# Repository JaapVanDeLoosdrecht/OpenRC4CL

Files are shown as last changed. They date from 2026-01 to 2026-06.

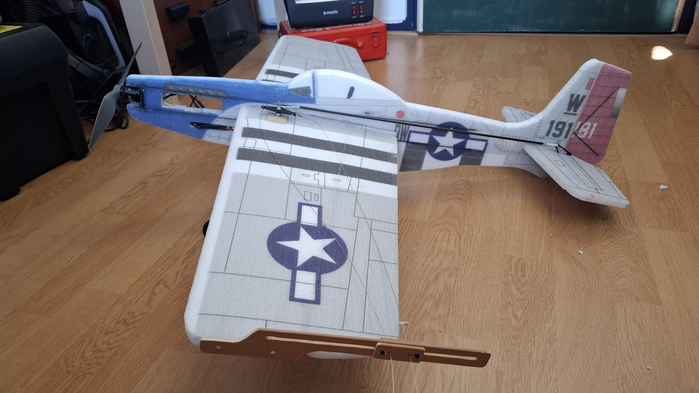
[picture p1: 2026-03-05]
photos/CL-E test model.jpg

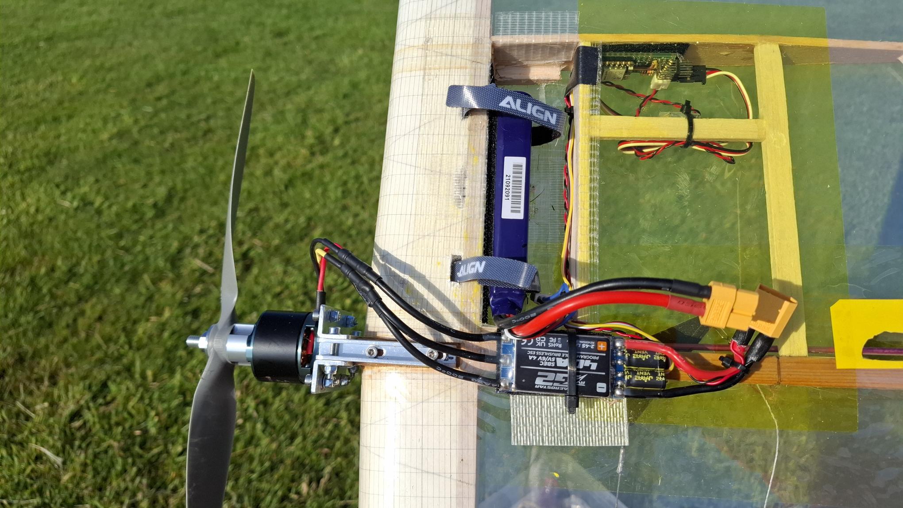
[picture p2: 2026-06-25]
photos/E-Combat 3.jpg

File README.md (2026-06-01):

# OpenRC4CL

Control Line (CL), also called U-Control, is a way of controlling model airplanes, see https://en.wikipedia.org/wiki/Control_line.

Low-cost DIY project based on low-cost ESP32C6s for expanding CL handles with Radio Control (RC) functions like throttle control, servos, timers, telemetry and failsafe.
Uses the ESP-NOW protocol transmitted via the 2.4 GHz Wi-Fi band.

One PCB for Tx, Rx and Timer.

The software is released as opensource under the MIT license.

Note this project is Work In Progress and is developed for ESP32 C6, does not need external antennas.

Feedback is welcome and I am open to ideas and/or collaboration.

See for discussion the (Dutch) Modelbouw forum https://www.modelbouwforum.nl/threads/openrc4cl-diy-lb-met-rc-functies.294026/ .

## NOTE: there are two PCBs:
- PCB V1 (4 channels) is tested
- PCB V2 is under design and not yet tested. It is smaller and for 2 channels.

## Functional overview OpenRC4CL.

Expanding CL handles with RC functions like throttle control, servos, timers, telemetry and failsafe.
Usage cases:

- Combat/trainer CL handle with throttle hold switch and small potmeter for setting throttle value between flights.
- Carrier/scale CL handle with continuous throttle 'trigger' control, throttle hold switch and 
  3 (two 3 states and one continuous) servo functions like for dropping hook, etc.
- etc.

Default servo pulse width [1000..2000] us @ 50 Hz, in software configurable.

Tx channels:

- 0: throttle potmeter
- 1: 3 position switch
- 2: potmeter or 3 position switch
- 3: potmeter or 3 position switch
- 4: potmeter or 3 position switch

Rx servo channels:

- 0: throttle
- 1: servo 1
- 2: servo 2
- 3: servo 3
- 4: servo 4

Special functions:

- kill switch on Tx
- check pairing Tx and Rx based on MAC address [planned soft MAC address]
- checksum on transmitted data
- failsafe if > 0.5 seconds connection lost OR TxBatt low:
  initiate throttle warning (like CLTimer) followed by stop engine and hold servos in last position
- telemetry with VBatt, VBatt low and RSI 
- throttle hold must be activated before Tx starts to transmit
- logging status and listing/setting configuration parameters of Tx andRx by bluetooth to smartphone
- Tx lipo voltage monitor (1 cell lipo) with low VBat warning
- low VBatt warning voltage setting (input potmeter) [3000..8*4350] mV, max 8S LiHV
- Rx ESC max 8S lipo voltage monitor, telemetry to Tx and beeper warning by low VBat
- max flight time parameter
- deadband throttle correction parameter
- exponential throttle curve (in software configurable) [planned]
- softstart throttle option (in software configurable) [planned]

Status codes for led and beeper (blink pulse in ms):
- Ok = 0 (off)
- WaitThrHold = 1000
- WaitConnection = 2000
- VBattLow and TxBattLow = 2000
- EndFlight = 4000
- Failsafe = 500
- Error = 200

## CLTimer [planned]

CLTimer is 'spinoff' project from components used for Tx and Rx projects in the OpenRC4CL repro.

Usage case: typical classic control line timer without remote RC functionality.

Inputs:

- parameters (analog input with potmeters):
	- delay start [0..60] secs
	- throttle level [0..100]%
	- runtime [0..8*60] secs
	- min VBatt [3000..8*4350] mV, max 8S LiHV
- VBatt (max 8S) (analog input)
- start/stop button (digital input)

Outputs:

- servo signal for ESC (analog output)
- status led (digital output)
- beeper (digital output)

Note if VBatt is not connected, only timer function avialable.

Phases (N and W are parameters configurable in software):  [WIP]

- connect battery and boot
- read parameters, log every 0.5 second parameters to serial monitor and BT 
- press button for 2 seconds to intiate 'ready_to_start', confirm with beep
- during ready_to_start
  - beep every 10 secs, last 10 sec every sec
  - abort ready_to_start if start button is pressed for 2nd time
    go to phase read parameters
- start engine and throttle timer, log every 0.5 second status to serial monitor and BT
- abort running if start button is (short) pressed for 2nd time
  go to phase read parameters
- W seconds before throttle timer expires OR if VBatt below min VBatt:
  issue for N (N < W) seconds throttle warnings (0.5 s half, 0.5 s normal throttle level) 
  (last W-N seconds full throttle level)
- stop engine 

Logging status by bluetooth or usb to smartphone or laptop.

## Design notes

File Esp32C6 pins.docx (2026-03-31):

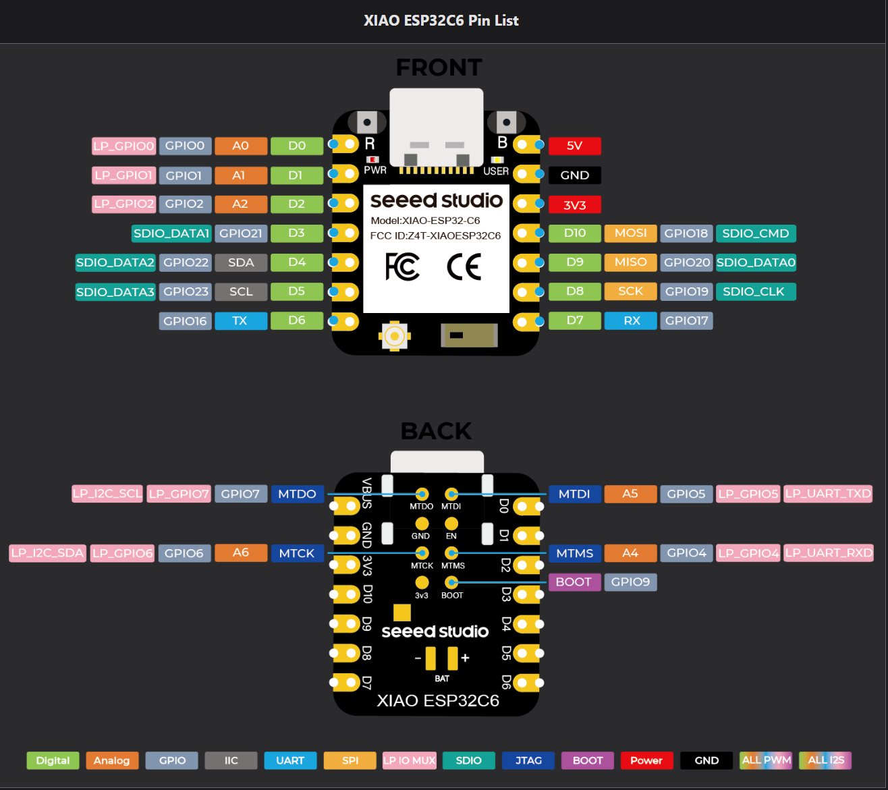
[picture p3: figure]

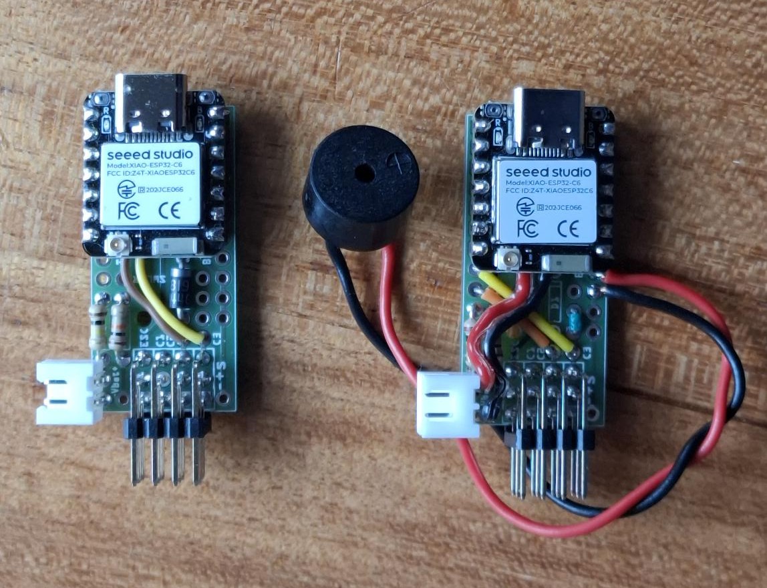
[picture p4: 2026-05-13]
photos/First Tx and Rx PCB V1.0.jpg

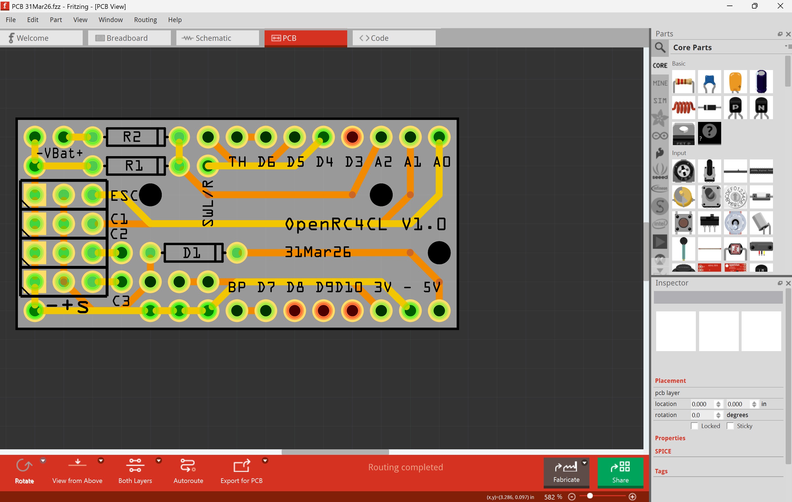
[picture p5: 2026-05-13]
photos/Fritzing PCB V1.0.jpg

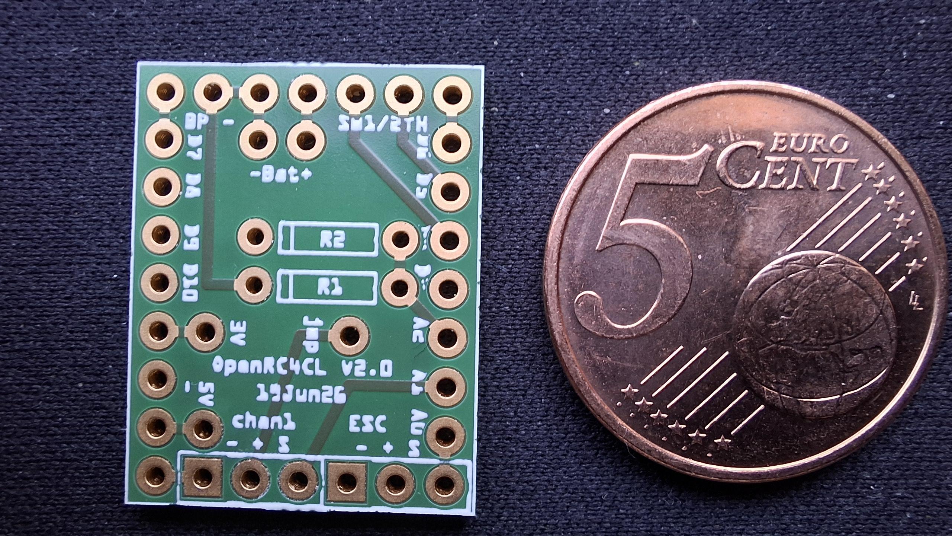
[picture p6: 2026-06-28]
photos/OpenRC4CL PCB V2.jpg

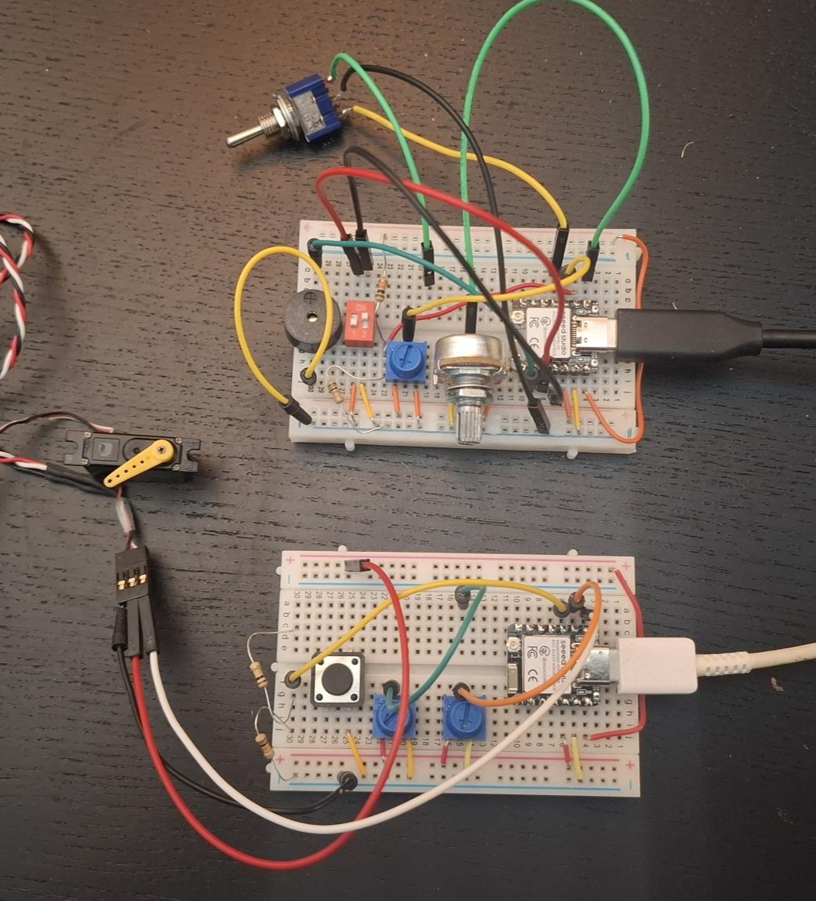
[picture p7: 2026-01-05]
photos/breadboard TxRx 15Dec25.jpg

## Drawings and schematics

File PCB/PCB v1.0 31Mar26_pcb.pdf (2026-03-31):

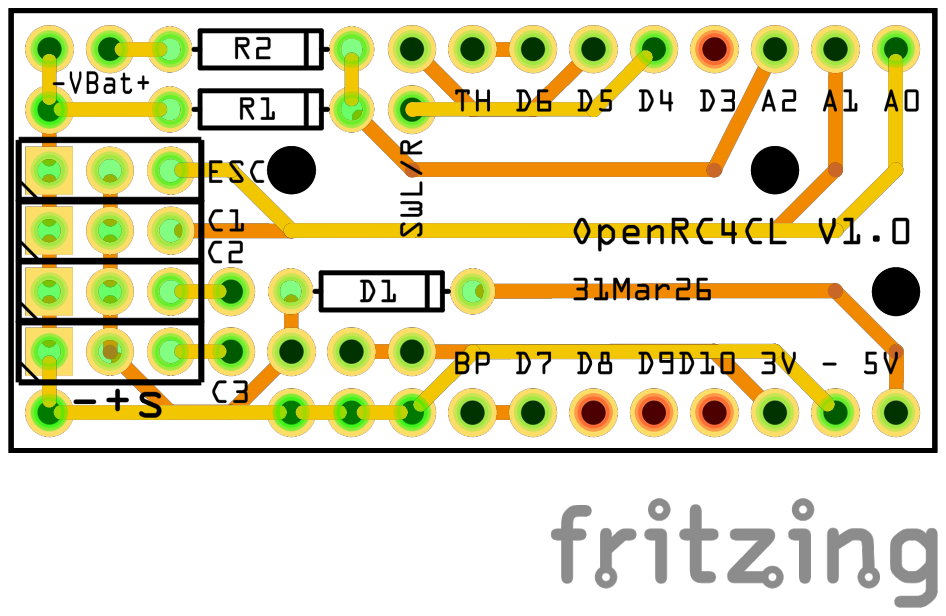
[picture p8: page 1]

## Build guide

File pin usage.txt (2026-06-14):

-----------------------------------------------------------------------
Pin usage PCB design V1.0:
Rx
- LED_BUILTIN: led Note LED_BUILTIN is reversed on C6
- A0: throttle=chan0 (output servo)
- A1: chan1 (output servo)
- A2: VBatt 8S lipo voltage monitor (input)
- D3:             
- D4:            
- D5:
- D6:
- D7:
- D8:
- D9: 
- D10:
- A4: chan2 (output servo)
- A5: chan3 (output servo)
- A6: chan4 (optional output servo, no PCM pad)

Tx:
- LED_BUILTIN: led: Note LED_BUILTIN is reversed on C6
- A0: throttle=chan0 (input potmeter)
- A1: 
- A2: Tx lipo voltage monitor (1 cell lipo) (input)
- D3:                                                                                                                                                                                                    
- D4: leftCh1  (input 3-pos switch)
- D5: rightCh1 (input 3-pos switch)
- D6: throttle hold (input switch)
- D7: beeper (output)
- D8:
- D9: 
- D10:
- A4: chan2 (input potmeter)
- A5: chan3 (input potmeter)
- A6: chan4 (optional input potmeter, no PCM pad)

CLTimer:
- LED_BUILTIN: led: Note LED_BUILTIN is reversed on C6
- A0: throttle=chan0 (output servo)
- A1: 
- A2: Tx lipo voltage monitor (1 cell lipo) (input)
- D3: 
- D4
- D5
- D6: start/stop button (input)
- D7: beeper (output)
- D8
- D9: 
- D10:
- A4: 
- A5: 
- A6: 

-----------------------------------------------------------------------
Pin usage Prototype board

Rx: Prototype board
- LED_BUILTIN: led Note LED_BUILTIN is reversed on C6
- A0: throttle (output servo)
- A1: chan1 (output servo)
- A2: chan2 (output servo)
- D3: (=A3?, does this exists? GPIO21? =(D3))
- D4: beeper (output)
- D5
- D6
- D7
- D8
- D9: select wifi 0   (input dipwsitch)
- D10: select wifi 1  (input dipwsitch)
- A4: chan3 (output servo)
- A5: low VBatt warning voltage or timer setting (input potmeter)
- A6: 8S lipo voltage monitor (input)

Tx: Prototype board
- LED_BUILTIN: led: Note LED_BUILTIN is reversed on C6
- A0: throttle (input potmeter)
- A1: Tx lipo voltage monitor (1 cell lipo) (input)
- A2: chan3 (input potmeter)
- D3: throttle hold (input switch)
- D4: leftCh1  (input switch)
- D5: rightCh1  (input swith)
- D6: leftCh2  (input switch)
- D7: rightCh2  (input switch)
- D8: beeper (output)
- D9: select wifi 0  (input dipwsitch)
- D10: select wifi 1  (input dipwsitch)
- A4: deadband throttle (input potmeter)
- A5: 
- A6: 

-----------------------------------------------------------------------
Connection Tx <---> Hold/Throttle

H = digital input with pullup R
T = analog input

4 pin audio   ---|---|---|--->   )---|---|---|---
function       -   H   T   +       -   H   T   +
color		   B   R   Y   W       B   R   Y   W
NOTE COLORS AUDIO CABLE ARE DIFFERENT ON DIFFERENT BATCHES???
			   
Phases in connecting:
 Tx || - | H | T | + ||
	||-------------------------
HT1 ||   |   |   | - || H  T  +
HT2 ||	 |   | - | H || T  +
HT3 ||   | - | H | T || +
HT4 || - | H | T | - ||

HT1: Tx T floating=0, Tx H floating=+ -> Hold on

HT2: Tx T floating=0 or +, Tx H floating=+ -> Hold on
Tx             T          +
HT             -          H                T              +

               |          |                |              |
               |          \                |              |
               |           \         ______|_____         |
               |__________|_________|            |________|
			                        |____________|
									
HT3: Tx T floating=0 or +, Tx H=+ -> Hold on
Tx             H          T                +
HT             -          H                T              +

               |          |                |              |
               |          \                |              |
               |           \         ______|_____         |
               |__________|_________|            |________|
			                        |____________|
								
HT4: everything connected right

-----------------------------------------------------------------------

8S ipo voltage measurement, div factor = 11

  0V          <= 3.3V       +1-8S
  |___ R 10K ___|___ R 100K __| 

------------------------------------------------------------------------
crimping pin notes with Engineer PA-24 crimping tool:
- first crimp electrial part and then isolation, note only strip small part
- if needed for thin wires double electrial part
- if needed make 'wings' for isolation parallel using front part of tool
- lipo balancer: W1.3 and W1.6
- servo: W1.3 and O1.4/O1.8 Note W and O

-------------------------------------------------
Tx PCB v1

NOTE COLORS AUDIO CABLE ARE DIFFERENT ON DIFFERENT BATCHES???
R cable       Black                       White          Red
Audio cable   Blue        Red             Yellow         White
               -          H                T              +

               |          |                |              |
               |          \                |              |
               |           \         ______|_____         |
               |__________|_________|            |________|
			                        |____________|

Throttle servo connector:
Tx chan0
Servo audio cable
  S     Yellow
  +     White
  -     nc
  
Throttle Hold servo connector:
Tx chan3
Servo audio cable
  S     Red
  +     nc
  -     Blue

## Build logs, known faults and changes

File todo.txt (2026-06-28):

Added/changed:
 
Todo:
- Rx-Vbatt-Critical
  3x esc warning and stop esc
- rx status ok if rx-batt low, tx side is correct
- if not yet done passwd ask first time for passwd
- Tx starts beeping after x mins not used
- Beep tx at connected
- exponential throttle curve
  can use (limited) floats?? lookup table?? N knee points with linear interpolation
- Vbat low blijven piepen en is te zacht voor in broek
  test bigger beeper

hall sensor or pot and output a 0.8–4V throttle signal
use simple crank and slider, max 180 degress and not linear
test 90 degrees rotation of 300 potmeter
Rack and pinion stl?

Design StateMachine and refactor code
Refactor CMD code use design pattern and make possible to add cmd Tx or Rx specific
like bindTab, status, etc

Switch to VS code for debugging and beter src control???

- generic logging (like blackbox) on C6
- Next Tx charge by usb with sealing cap.
  Is this possible, needs 'step' in wall for access usb connector?
- Tx led en laad connector (balance?)
- Lost count tx klopt niet is altijd zero

- todo test A4 (MTMS) to C2 and A6 (MTCK) to C3
- note is difficult to implement: beep 1x if killswitch deactivated
  idea: add status InfoBeep for this purpose
  in update: only if status==InfoBeep only go to StatusOk if beep 'expired'

- test with C6 devkit debugging on new breadboard, use wire or dipswitch for TH
- test new software on prototype boards
  Rx: A0 thr, A2 vbat
  Tx: A0 esc, A1 vbat, D3 TH, D8 beep
- ?? softstart option for CLtimer and combat handle (= startup ramp %)
  rampup time if starting from zero
   most ESCs have a similar function

- Small tx pcb: 
  use JST PH connector for VBat or solder connection for JST-PH red connector
  use possibilty for horizontal Esc servo connector
  Ideas: 
  - use on both side of esp JST 2.0 SH connectors max 7 pins, is it possible to add connector with 1mm space in Frizting 
  - special Rx pcb, one side with 2 horizontal servo connector (Esc and chan1)
- idea? No PCB version for simple (TH + THR + hook) Tx handle?? Only two Rs needed.
  every connection its own wire? 
  using flat cable with connector?
  small form factor add-onn box for handle (ESP + 2 switches + potmeter) 
  same idea for simple Rx?? with flat cable 
  flat flexible cable (ribon cable) pitch JST SH 1.0? mm: 
  - minimal 11: 5v, 3.3V, GND, TxBatt+, TxBatt-, Pot/Esc(A0), Chan1(A1), VBatt+(A2), TH(D6), SW1(D5), Beep(D7)
    extra GNDs?
  - extra or solder direct to C6: SW2(D4), Chan2(A4), Chan3(A5), 
  JST 2.0 SH 12 pins is too big??, split in multiple cables?
  https://www.amazon.com/Connector-Housing-Connectors-Controller-Pre-Crimped/dp/B0DH29DLMT?th=1 (only female?)
  https://www.amazon.com/JST-PH-Connector-Silicone-Cables-Female/dp/B0DMZK9CJR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
  https://www.amazon.com/JST-PH-Connector-Silicone-Cables-Female/dp/B0DMW7FPCH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 100Hz?

ON OFF ON SPDT switch wiring
                 Throw 1 ----- GND
                 Throw 2 ----- 3.3V
                 Common  ----- ADC pin
3.3V ----[ Rtop ]----+----[ Rbottom ]---- GND
                      |
                    ADC pin
	Common → ADC pin
	One end → GND
	Other end → 3.3 V
	Middle position = OFF → no connection → ADC only sees the resistor divider.
Resulting voltages
	Position 1 (to GND): ADC ≈ 0" V" (switch dominates, low impedance to GND)
	Middle (OFF): ADC ≈ 1.65" V" (pure divider)
	Position 3 (to 3.3 V): ADC ≈ 3.3" V" (switch dominates, low impedance to VCC)
Now you truly get three stable, well separated levels.
Use 20K Rs!

- move repro to https://codeberg.org/??
- esp-now analyser https://wiki.wireshark.org/ESP_Preferences

CLTimer: 
- Update to latest version of OpenRC4CL_util.h
  Beeper warning signal N secs before starting engine
  Abort starting sequence and running with button
- softstart option for CLtimer and combat handle (= startup ramp %)
  rampup time if starting from zero

fase2:
- exponential throttle
- use state machine to keep track of status and actions
- for documentation: differentiate between to thr warning systems
  note warning are NOT synchronised (yet), a protocol is needed
  - Tx: beep warning after maxTime expired
  - Rx: esc warning before maxTime expires and kill engine at maxTime
- note: chan 2/3/4 can be used for on/switch
- pinExternLed D8/9/10? or use chan3?? or only led indicating bat connected?
- add R1 and R2 to NVS, can be used for tuning V calib usig ohm meter
- this needed is only needed if rearranging order is needed
  Rename class Switch to SwitchDI and make SwitchAI
  Note dangling middle=dangling 0V, L/R= 1.65V/3.3V, use Tx software to put in 'ascending order'
- alternative Rx: create NVS param and use map(pin table)
  rearrange using: int* map = &rc.chan1  (is ptr to int[4])
- 2 or 3 position switches on Tx are also possible using reading the normal channels and analoge input
  using two Rs for voltage divisor
- add channel mapping on Rx default "[0,1,2,3,4]"
  map channel order right after packet is received
- pair using wifi breadcast mode pair ble_name -> mac_addr
- Tx for all chans add 
  - offset middle position
  - min and max value
- new Failsafe throttle implementation: always for 2(?) sec toggle 0.5 sec to half power and than TH, no need for timer only wall clock
- soft mac address for Rx (and Tx??)
- (paper display on TX)

(fase 3:
- use IMU as crash sensor to kill engine
- governor for throttle
- see for ideas https://www.keithrenecle.co.za/Electric%20CL.htm#Govtimerinfo 
- https://howtomechatronics.com/how-it-works/how-brushless-motor-and-esc-work/
- https://www.digikey.com/en/articles/controlling-sensorless-bldc-motors-via-back-emf
- https://www.rcgroups.com/forums/showthread.php?1006124-Brushless-rpm-Sensor
- hall sensor??
- idea measure freq zero crossing
- pcb https://fritzing.org/learning/tutorials/designing-pcb/
  https://community.aisler.net/t/our-simple-pricing/102
)

Changed:

Idea for mac table (if bind with broadcast is not possible)

class MAC_tab {
public:
  MAC_tab() {};  read from nms  (own space with name mac)
  // not needed??  int nrElms() { return nr; }
  int add(char* name, char* mac) {
    // check max elems
    tab[nr].name = strcpy(name); ?? check length smaller than max
    tab[nr].mac = strcpy(mac); ??  check length exactly
	add to nvs 
    return nr++;
  }
  char* mac(char* name) {
    find name in tab and return mac
  }
private:
  struct MAC_ELM{ char name[11]; char mac[17]};
  int nr = 0;
  MAC_ELM tab[16];
}

- bind devName -> set macPeer  and reboot
- devNames -> list devName macAdr,  ..., ...
- cmd addPeer namePer macPeer
- cmd remvePeer namePer # move all 'higher idx' peer one postion up in table
- use extra NVS namePeers

Zero allocation version using fixed size

struct Entry {
    char key[32];
    char value[32];
};

Entry table[] = {
    { "SSID",     "MyWiFi" },
    { "Password", "SuperSecret" },
    { "Mode",     "Station" }
};

const size_t tableSize = sizeof(table) / sizeof(table[0]);

const char* getValueByKey(const char* key) {
    for (size_t i = 0; i < tableSize; i++) {
        if (strcmp(table[i].key, key) == 0) {
            return table[i].value;
        }
    }
    return nullptr;
}

bool setValueByKey(const char* key, const char* newValue) {
    for (size_t i = 0; i < tableSize; i++) {
        if (strcmp(table[i].key, key) == 0) {
            strncpy(table[i].value, newValue, sizeof(table[i].value) - 1);
            table[i].value[31] = '\0';
            return true;
        }
    }
    return false;
}

void printTable() {
    for (size_t i = 0; i < tableSize; i++) {
        Serial.print("Key: ");
        Serial.print(table[i].key);
        Serial.print("  Value: ");
        Serial.println(table[i].value);
    }
}

void setup() {
    Serial.begin(115200);

    printTable();

    Serial.println("\nChanging Mode...");
    setValueByKey("Mode", "AccessPoint");

    Serial.println("\nNew table:");
    printTable();

    Serial.println("\nLookup SSID:");
    const char* ssid = getValueByKey("SSID");
    if (ssid) Serial.println(ssid);
}

void loop() {}

Define a POD style class (or struct)
To store an object as a blob, it must be trivially copyable (no pointers, no virtual methods, no dynamic memory).

struct DeviceConfig {
    uint32_t version;
    int32_t threshold;
    float gain;
    bool enabled;
};

#include <Preferences.h>

Preferences prefs;

DeviceConfig config = {
    .version = 1,
    .threshold = 42,
    .gain = 0.75f,
    .enabled = true
};

void saveConfig(const DeviceConfig &cfg) {
    prefs.begin("app", false);  // RW mode

    prefs.putBytes("config", &cfg, sizeof(DeviceConfig));

    prefs.end();
}

bool loadConfig(DeviceConfig &cfg) {
    prefs.begin("app", true);  // read-only

    size_t size = prefs.getBytesLength("config");
    if (size != sizeof(DeviceConfig)) {
        prefs.end();
        return false;  // no valid config stored
    }

    prefs.getBytes("config", &cfg, sizeof(DeviceConfig));

    prefs.end();
    return true;
}

void setup() {
    Serial.begin(115200);

    DeviceConfig loaded;

    if (loadConfig(loaded)) {
        Serial.println("Loaded config:");
        Serial.printf("version=%u threshold=%d gain=%.2f enabled=%d\n",
                      loaded.version, loaded.threshold,
                      loaded.gain, loaded.enabled);
    } else {
        Serial.println("No valid config found, saving defaults...");
        saveConfig(config);
    }
}

void loop() {
}

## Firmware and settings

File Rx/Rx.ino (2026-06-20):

/* 
Rx OpenRC4CL 20 June 2026

MIT license

Copyright 2026 Jaap van de Loosdrecht

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
THE SOFTWARE IS PROVIDED “AS IS”, WITHOUT WARRANTY OF ANY KIND, EXPRESS OR IMPLIED, 
INCLUDING BUT NOT LIMITED TO THE WARRANTIES OF MERCHANTABILITY, FITNESS FOR A PARTICULAR PURPOSE AND NONINFRINGEMENT. 
IN NO EVENT SHALL THE AUTHORS OR COPYRIGHT HOLDERS BE LIABLE FOR ANY CLAIM, DAMAGES OR OTHER LIABILITY, 
WHETHER IN AN ACTION OF CONTRACT, TORT OR OTHERWISE, ARISING FROM, OUT OF OR IN CONNECTION WITH THE SOFTWARE 
OR THE USE OR OTHER DEALINGS IN THE SOFTWARE.
*/

// NOTE: this is only tested on XIAO ESP32-C6, use partition schema NO OTA (2MB APP/2MB SPIFFS)
// RX com7 (proto=9) black 2nd usb

#include <MacAddress.h>
#include <WiFi.h>
#include <limits.h>
#include "OpenRC4CL_util.h"
#include "secret.h" // NOTE: file secret.h contains mac adrs used by developper and is NOT part of distro, comment out this line!!!
#ifndef OpenRC4CL_SECRET
BindElm txTab[] = { {"Tx-OpenRC4CL", "00:00:00:00:00:00"},   // modify with your devName and mac address of Tx or use serial CMDs
//                  {"Tx-name2", "00:00:00:00:00:00"},       // you can add more Txs
                  };
#endif

// system
const unsigned long FAILSAFE_TIME = 500;    // ms
const int lipoDivR1 = 10000;                // R1 lipo voltage divider, max 8S
const int lipoDivR2 = 100000;               // R2 lipo voltage divider
const int maxBinds = 10;                    // max nr of Txs
// user settings (NVS params)
String devName = "Rx-OpenRC4CL";            // modify with your Rx devName and or use serial CMD
String devPeer = txTab[0].devName; 
String macPeer(txTab[0].mac); 
String passwd = "123";
String date = buildDate();
int wifiChan = 6;                           // [1..13]
int maxTime = 5*60;                         // seconds
int vBattLow = 3500;                        // mV
int escWarn = 0;                            // [0,1] if 1 issue Esc warnings end stop engine at end of flight 
int nrWarns = 3;                            // number of Esc warnings before stopping engine
int stopEngine = 5;                         // nr of secs to stop engine after last Esc warning
int minThrottle = TxMidPulse;               // min throttle value to start timer, 0 = no restart timer 
int nrPackets = 100;                        // nr packets (50 Hz) to receive for telemetry and logging
int logging = 1;                            // 1: log status, 0: no log
int vBatt = 0;                              // 0 = no vBatt connected, 1 = vBatt connected, to avoid floating analog inputs warnings
int ch1Left = 1000;                         // pulses in us for 3 pos switch channel 1 
int ch1Middle = 1500;
int ch1Right = 2000;

NVS* buildNVS(Logger *log) {
  const int max_nvs_params = 32; 
  NVS* nvs = new NVS(NVSNameSpace, max_nvs_params, log); 
  nvs->add(NVS_STR(devName, true));
  nvs->add(NVS_STR(devPeer, true));
  nvs->add(NVS_STR(macPeer, true));
  nvs->add(NVS_STR(passwd, true));
  nvs->add(NVS_STR(date, false));
  nvs->add(NVS_INT(wifiChan, true, 1, 13));
  nvs->add(NVS_INT(maxTime, true, 10, 10*60));
  nvs->add(NVS_INT(vBattLow, true, 3000, 8*4350));
  nvs->add(NVS_INT(escWarn, true, 0, 1));
  nvs->add(NVS_INT(nrWarns, true, 0, 10));
  nvs->add(NVS_INT(stopEngine, true, 0, 10));
  nvs->add(NVS_INT(minThrottle, true, TxMinPulse, TxMaxPulse));
  nvs->add(NVS_INT(nrPackets, true, 50, 1000));
  nvs->add(NVS_INT(logging, false, 0, 1));
  nvs->add(NVS_INT(vBatt, true, 0, 1));
  nvs->add(NVS_INT(ch1Left, true, TxMinPulse, TxMaxPulse));
  nvs->add(NVS_INT(ch1Middle, true, TxMinPulse, TxMaxPulse));
  nvs->add(NVS_INT(ch1Right, true, TxMinPulse, TxMaxPulse));
  return nvs;
}

class Rx : public RcPeer {  
public:
  Rx(MacAddress mac_tx, uint8_t channel, wifi_interface_t iface, const uint8_t *lmk, Logger *log) : RcPeer(mac_tx, channel, iface, lmk) { 
    failsafe(); 
    logger = log;
    logStatus();
  }
  void onReceive(const uint8_t *data, size_t len, bool broadcast) { 
    struct TxData rc = *(struct TxData *)data;  // copy received data
    unsigned long now = millis();
    command(rc, now);
    telemetry(rc, now);
    status.value = (timer.elapsed() ? Status::EndFlight : (packetsLost > 0) ? Status::Error : (waitThrHold) ? Status::WaitThrHold: Status::Ok);
  }
  void update() {
    if (connected) {                       // check failsafe
      unsigned long last = timeLastTx;     // copy of last before geting now, this function can be interupted
      unsigned long now = millis();
      if ((now - last) > FAILSAFE_TIME) {  // note check can be interrupted by callback, abs doesn't work on unsigned
        failsafe();
        waitThrHold = true;                // reset from FailSafe with TH
        if (status.value != Status::Failsafe) {
         status.value = Status::Failsafe;
         logger->printf("FAILSAFE!!!!\n"); // log once
        }
        timeLastTx = now;                  // another test in FAILSAFE_TIME
      }
    }
    led.set(status.pulse()); led.update(); 
  }
protected:
  void logStatus() { 
    if (logging)   
      logger->printf("Rx:%s vbatt:%d t:%d maxt:%d lost:%d errors:%d\n", 
                      status.str(), rxBatt.read(), timer.secondsLeft(), maxTime, totalLost, errors);
  }
  void command(struct TxData &rc, unsigned long now) {
    if (CheckSum(rc) == rc.checkSum) { 
      if (!connected) { connected = true; timer.start(); status.value = Status::Ok; }  // timer can be reset using first minimal throttle command
      timeLastTx = now;
      if (rc.throttle == TxThrottleHoldPulse) waitThrHold = false;  // wait for (first) TH at start Rx
      thrLast = throttle.writeTx(waitThrHold ? throttle.failSaveValue() : rc.throttle);
      rc.chan1 = UpdateSwitchCh1(rc.chan1);
      chan1.writeTx(rc.chan1); chan2.writeTx(rc.chan2); chan3.writeTx(rc.chan3); chan4.writeTx(rc.chan4);
      if (rc.id < 100) {  // new Tx 
        timer.start(); status.value = Status::Ok;
        packetsLost = 0; lastId = -1; count = -1; 
      }    
      if (lastId > 0) packetsLost += rc.id - lastId - 1;
      lastId = rc.id;
    } else {
      packetsLost++; totalLost++;
    }
  }
  void telemetry(struct TxData &rc, unsigned long now) {
    if ((count == -1) && (rc.id % nrPackets != 0)) return;  // new Rx or Tx, sync id to multiple of nrPackets
    if (++count >= nrPackets) {  
      int rsi = max(nrPackets-packetsLost,0);
      struct Telemetry tel = {0, rc.id, status.value, rxBatt.read(), vBattLow, rsi, timer.secondsLeft(), totalLost, errors};
      tel.checkSum = CheckSum(tel);
      if (!send_data((const uint8_t *)&tel, sizeof(tel))) errors++;
      int avg_time = (int)(now - timeLast1st) / nrPackets;
      if (logging)  
        logger->printf("Rx:%s vbatt:%d thr:%d ch1:%d ch2:%d ch3:%d ch4:%d ms:%d rsi:%d t:%d maxt:%d lost:%d errors:%d\n", 
                        status.str(), rxBatt.read(), thrLast, rc.chan1, rc.chan2, rc.chan3, rc.chan4, avg_time, rsi, 
                        timer.secondsLeft(), maxTime, totalLost, errors);
      count = packetsLost = 0;
      timeLast1st = now;
    }
  }
  void failsafe() {
    throttle.failsafe(); chan1.failsafe(); chan2.failsafe(); chan3.failsafe(); chan4.failsafe(); 
  }
protected:
  int UpdateSwitchCh1(int value) {
    switch (value) {
      case TxMinPulse: return ch1Left;
      case TxMidPulse: return ch1Middle;
      case TxMaxPulse: return ch1Right;
      default: return value;
    }
  }
private:
  RcTimer timer{maxTime};
  Throttle throttle{pinThrottle, &timer, minThrottle, maxTime, escWarn, nrWarns, stopEngine};
  RcServo chan1{pinCh1, TxMinPulse, TxMaxPulse, 0, -1};
  RcServo chan2{pinCh2, TxMinPulse, TxMaxPulse, 0, -1};
  RcServo chan3{pinCh3, TxMinPulse, TxMaxPulse, 0, -1};
  RcServo chan4{pinCh4, TxMinPulse, TxMaxPulse, 0, -1};
  VoltageDiv rxBatt{(vBatt) ? pinVBatt : PIN_NOT_USED, lipoDivR1, lipoDivR2};
  Status status{Status::WaitTxRx};
  Led led{pinLed, status.pulse(), true}; 
  bool connected = false, waitThrHold = true;
  unsigned long timeLastTx = 0, timeLast1st = 0;  // time last 1st packadge;
  int thrLast = -1, lastId = -1, count = -1, packetsLost = 0, totalLost = 0, errors = 0;
  Logger *logger = 0;
};

Rx *rx = 0;                   // initialisation must be in setup 
CMD* cmd = 0; 
BindTab* bindTab = 0;

void setup() {
  //nvs_erase();
  String dn = GetStringNVS(NVSNameSpace, "devName");
  if (dn != String("")) devName = dn;
  Serial.begin(115200);
  SerialBLE.begin(devName);
  bindTab = new BindTab(NVSNameSpace, maxBinds, sizeof(txTab)/sizeof(BindElm), txTab);
  Logger *logger = new Logger;    // Serial and BLE logger
  NVS* nvs = buildNVS(logger);
  cmd = new CMD(nvs, logger, bindTab);
  WiFi.mode(WIFI_STA); WiFi.setChannel(wifiChan);
  logger->printf("OpenRC4CL %s Rx=%s channel=%d Tx=%s\nMAC-Rx=%s MAC-Tx=%s\n", 
                  OpenRC4CL_VERSION, devName.c_str(), wifiChan, devPeer.c_str(), WiFi.macAddress().c_str(),macPeer.c_str());
  cmd->list(); cmd->bindtab();
  rx = new Rx(MacAddress(macPeer), wifiChan, WIFI_IF_STA, nullptr, logger);
  while (!WiFi.STA.started()) delay(100);
  if ((!ESP_NOW.begin()) || (!rx->add_self())) {
    logger->printf("Failed to initialize Rx, rebooting in 2 seconds...\n");
    delay(2000); ESP.restart();
  }
}

void loop() {
  rx->update();
  cmd->update(); 
}

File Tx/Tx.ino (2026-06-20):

/* 
TX OpenRC4CL 20 June 2026

MIT license

Copyright 2026 Jaap van de Loosdrecht

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
THE SOFTWARE IS PROVIDED “AS IS”, WITHOUT WARRANTY OF ANY KIND, EXPRESS OR IMPLIED, 
INCLUDING BUT NOT LIMITED TO THE WARRANTIES OF MERCHANTABILITY, FITNESS FOR A PARTICULAR PURPOSE AND NONINFRINGEMENT. 
IN NO EVENT SHALL THE AUTHORS OR COPYRIGHT HOLDERS BE LIABLE FOR ANY CLAIM, DAMAGES OR OTHER LIABILITY, 
WHETHER IN AN ACTION OF CONTRACT, TORT OR OTHERWISE, ARISING FROM, OUT OF OR IN CONNECTION WITH THE SOFTWARE 
OR THE USE OR OTHER DEALINGS IN THE SOFTWARE.
*/

// NOTE: this is only tested on XIAO ESP32-C6, use partition schema NO OTA (2MB APP/2MB SPIFFS)
// Tx com5 (proto=8) white 1st usb 

#include <MacAddress.h>
#include <WiFi.h>
#include <limits.h>
#include "OpenRC4CL_util.h"  
#include "secret.h" // NOTE: file secret.h contains mac adrs used by developper and is NOT part of distro, comment out this line!!!
#ifndef OpenRC4CL_SECRET
BindElm rxTab[] = { {"Rx-OpenRC4CL", "00:00:00:00:00:00"},   // modify with your devName and mac address of Rx or use serial CMDs
//                  {"Rx-name2", "00:00:00:00:00:00"},       // you can add more Rxs
                  };
#endif

// system
const int deadBandMax = ThrHoldDelta-10;    // deadband delta for throttle, no overleap with TH
const int deadBandMin = -deadBandMax;    
const int lipoDivR1 = 10000;                // R1 lipo voltage divider, max 5V usb, div=2
const int lipoDivR2 = 10000;                // R2 lipo voltage divider
const int maxBinds = 10;                    // max nr of Rxs
// user settings (NVS params)
String devName = "Tx-OpenRC4CL";            // modify with your Tx devName and or use serial CMD
String devPeer = rxTab[0].devName; 
String macPeer(rxTab[0].mac); 
String passwd = "123";
String date = buildDate();
int wifiChan = 6;                           // [1..13]
int deadBand = 0;                           // deadband delta for TH low
int txBattLow = 3500;                       // min voltage for Tx lipo
int nrWarns = 10;                           // number beeps if TxBattLow or timer is expired number 
int logging = 1;                            // 1: log status, 0: no log
int nrChans = 2;                            // nr of channels used [2..5], to avoid floating analog inputs warnings
int ch1Switch = 1;                          // pins used for ch1 switch: 0 = pinLeftCh1, 1 = pinRightCh1, 2 = both pins
int vBatt = 1;                              // 0 = no vBatt connected, 1 = vBatt connected, to avoid floating analog inputs warnings

NVS* buildNVS(Logger *logger) {
  const int max_nvs_params = 32; 
  NVS* nvs = new NVS(NVSNameSpace, max_nvs_params, logger); 
  nvs->add(NVS_STR(devName, true));
  nvs->add(NVS_STR(devPeer, true));
  nvs->add(NVS_STR(macPeer, true));
  nvs->add(NVS_STR(passwd, true));
  nvs->add(NVS_STR(date, false));
  nvs->add(NVS_INT(wifiChan, true, 1, 13));
  nvs->add(NVS_INT(deadBand, true, deadBandMin, deadBandMax));
  nvs->add(NVS_INT(txBattLow, true, 3000, 4350));
  nvs->add(NVS_INT(nrWarns, true, 1, 20));
  nvs->add(NVS_INT(logging, false, 0, 1));
  nvs->add(NVS_INT(nrChans, true, 2, 5));
  nvs->add(NVS_INT(ch1Switch, true, 0, 2));
  nvs->add(NVS_INT(vBatt, true, 0, 1));
  return nvs;
}

class Tx : public RcPeer {
public:
  Tx(MacAddress mac_rx, uint8_t channel, wifi_interface_t iface, const uint8_t *lmk, Logger *log):
    RcPeer(mac_rx, channel, iface, lmk) { logger = log; }
  void wait4ThrHold() {
    status.value = Status::WaitThrHold;
    logStatus(); 
    while (hold.readPos() != Thr_Hold) { delay(100); statusUpdate(); }
    status.value = Status::WaitTxRx;
    logStatus();
  }
  void update() { sendTx(); statusUpdate(); }
  void onReceive(const uint8_t *data, size_t len, bool broadcast) {
    connected = true;
    lastTelm = millis();
    struct Telemetry tel = *(struct Telemetry *)data;
    if (CheckSum(tel) != tel.checkSum) { 
      status.value = Status::Error; errors++;
      logStatus();
      return;
    }
    if (tel.status == Status::WaitThrHold) {
      status.value = Status::WaitThrHold; 
    } else {
      bool vBattLow = (tel.vBat > vbatThr) && (tel.vBat < tel.vBatLow);
      if (!(endFlight = vBattLow || (tel.time_left < 0))) {
        status.value = Status::Ok;                                                                                                                                                                                              ;
        beepEndFlight = false; // needed if Rx is reset after end of flight
      } else {
        status.value = (vBattLow) ? Status::RxBattLow : Status::EndFlight;
      }
    }
    if (logging) 
      logger->printf("[Tx:%s bat:%d thr:%d err:%d] [Rx:%s vBat:%d vLow:%d rsi:%d time:%d lost:%d err:%d]\n", 
                     status.str(), txBatt.read(), readThrottle(), errors, 
                     Status::val2str(tel.status), tel.vBat, tel.vBatLow, tel.rsi, tel.time_left, tel.totalLost, tel.errors);
  }
protected:
  int readThrottle() {
    throttle.setMinMax(TxMinPulse + deadBand);  // deadBand can be changed by CMD
    return (hold.readPos() == Thr_Hold) ? TxThrottleHoldPulse : throttle.read();
  }
  void sendTx() {
    struct TxData rc{0, ++id, readThrottle(), chan1.read(), chan2.read(), chan3.read(), chan4.read()}; 
    rc.checkSum = CheckSum(rc);
    if (send_data((uint8_t *)&rc, sizeof(rc)) || !connected) {   
      lastId = id;
    } else {
      errors++;
    }  
    unsigned long now = millis();  // check still connected
    if ((now - lastTelm) > 5000) {  // note check can be interrupted by callback, abs doesn't work on unsigned
      connected = false; errors = 0;
      if (status.value != Status::WaitTxRx) {
        status.value = Status::WaitTxRx;
        logStatus();  // only log once
      }
    }
    statusUpdate();
  }
  void logStatus() { if (logging) logger->printf("[Tx:%s bat:%d thr:%d err:%d]\n", status.str(), txBatt.read(), readThrottle(), errors); }
  void statusUpdate() {  // update status for led and beep
    if (!endFlight) {
      int txV = txBatt.read();                             // Check txV here because Rx could be off and so no telemetry
      if (endFlight = (txV > vbatThr) && (txV < txBattLow)) {  // tBatt ~ 0 if usb powered without lipo
        status.value = Status::TxBattLow;
      }
    }
    led.set(status.pulse()); led.update(); 
    if (endFlight) {
      if (!beepEndFlight) { 
        beep.set(status.pulse(), nrWarns); 
        beepEndFlight = true; 
      }  
    } else {
      int p = status.pulse();
      beep.set((p == Status::Ok) ? p = -1 : p);            // no beep if Ok
    }
    beep.update(); 
  }
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

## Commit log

2025-10-07 V0.03
    CL Timer and Throttle Hold added
2025-10-10 0.0.5
    Added throttle hold.
    Failsafe triggers throttle warning signal before stopping.
    Added support for reversed throttle.
    [CLtimer.ino, Rx.ino, Tx.ino]
2025-10-11 0.0.6
    blink buildin led for status Rx and Tx
2025-10-12 0.0.7
    added blink buildin led for status CLTimer
2025-10-20 0.0.8
    - Tx wait for Throttle Hold until activate Tx
    - Refactor class Led
2025-10-25 0.0.9
    Base class Blink for Led and Beep added
    Beeper added
2025-10-25 0.0.10
    Tx: warning when ThrHold is off when powering up
    if Rx restarts Tx should reset beep_end_flight
    added chan2 and chan3
    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
    [CLtimer.ino, Rx.ino, Tx.ino]
2025-10-26 0.0.11
    concept for class LipoV
    [Lipo voltage.xlsx]
2025-11-30 0.0.15
    - remove max thr from Rx, have always on pot meter on Tx also for combat
    - display Tx log TH and Thr value before telemetry
    - Rx to TH if Rx turned on and first msg (after checksum check) is not TH
    leave this mode after TH is received from Tx
    - added PIN_NOT_USED and default action for all sensors and actuators
    - new struct Status
2025-12-07 0.0.16
    - bugfix esc thr warning
    - added to class Throttle EscWarn to dis/en_able Esc throttle warning
    - added vbatt and low vbatt to telemetry, vbatt < low vbatt -> buzzer
    - added batt Tx and warning/error
    - added nr error in telemetry and logging for both Tx and Rx
    [Rx.ino, Tx.ino]
2025-12-12 0.0.17
    - class DipSwitch for max 4 pins or use array and nrSwitches
    - use 2 dipswitches to select 4 different wifi channel nrs in Rx and Tx (chan 1, 6, 11,13)
    - Tx added deadband correction for throttle
    - reverse (and check rotation direction) polarity of instel pots
    - reset with TH needed after FailSave
    - deadband correction should be applied only to lower range throttle, not top
    [Rx.ino, Tx.ino]
2026-01-10 0.0.21
    Added Rx Status to Telemetry
    Bug fix status led for Status:Ok
    Bug fix beeper for status Ok
    moved *.jpg to photo directory
    [Lipo voltage.xlsx]
2026-03-20 0.1.1
    - added Cmds default, reboot and lock
    - add min and max values to NVS param config
    - make CMDs more robust, like set param <no value> or illegal string for int, etc
    - extended to 5 chans
    [Rx.ino, Tx.ino]
2026-03-21 0.1.2
    - changed Tx and Rx macadr to string
    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
    [Rx.ino, Tx.ino, tmp.ino]
2026-03-31 0.1.6
    - removed PSTRs
    - moved Tx and Rx consts to NVS
    - unified PCB v1.0 for Tx, Rx and Timer
    [PCB 31Mar26.fzz]
2026-04-01 1.0.7
    - sync version nrs PCB and SW like: PCB 1.0 = SW 1.0.xx
    - refactored CMD.exec
    - added build date to NVS
    - moved pin definitions to util.h (PCB dependent)
2026-04-02 1.0.8
    - refactor Tx and Rx for logger, CMD and NVS
    - bug fix Rx= EndOfFlight -> TX give TxBatLow
    [Rx.ino, Tx.ino]
2026-05-29 1.0.12
    Added untested concept PCB V2
    [PCB v.2.0 28May26.fzz, PCB v1.0 31Mar26.fzz, Rx-1.fzz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]
2026-06-01 1.0.12
    Added
    - basic loging Tx/Rx status if peer is not connected
    - cmd log on/off
    - bugfix for Tx.connected
    - refactor Rx.failsafe
    - primitive bind using cmd mac and set macPeer 00:00:00:00:00:00
    - rearranged wiring protoboard to PCB standard
    [Rx.ino, Tx.ino]
2026-06-03 1.0.13
    - Tx mode TwoChans added
    - Tx mode chan1 for 2 or 3 pos switch added
2026-06-05 1.0.14
    - refactor class Switch
    - added NVS params nrChans and vBatt, to avoid floating analog inputs
    - added Rx nvs ch1Left = 1000, ch1Right = 2000, ch1Middle = 1500
    - logging will always restart at (re)boot
    - update PCB v2
    [PCB v.2.0 28May26.fzz, PCB v.2.0 5Jun26.fzz]
2026-06-14 1.0.15
    - Added NVS presistant (non-editable) parameters
    - Servo reads current position at boot for initialising _last postion
2026-06-14 1.0.16
    - added NVSNameSpace as global const to OpenRC4CL_util.h
    - fixed devName bug, is now read from NVS if available
    - added bindtab and bind command
    [Rx.ino, Tx.ino]
2026-06-20 1.0.17
    Added/changed:
    - Status::VBattLow changed to RxBattLow
    - refactor BindTab
    Allocate all mem at booth and copy values to memory during add
    - Preferences pref; is now used local in function to avoid multiple open versions
    - added cms addbind and removebind
    - extend help info
    [PCB v.2.0 19Jun26.fzz, PCB v.2.0 5Jun26.fzz]
